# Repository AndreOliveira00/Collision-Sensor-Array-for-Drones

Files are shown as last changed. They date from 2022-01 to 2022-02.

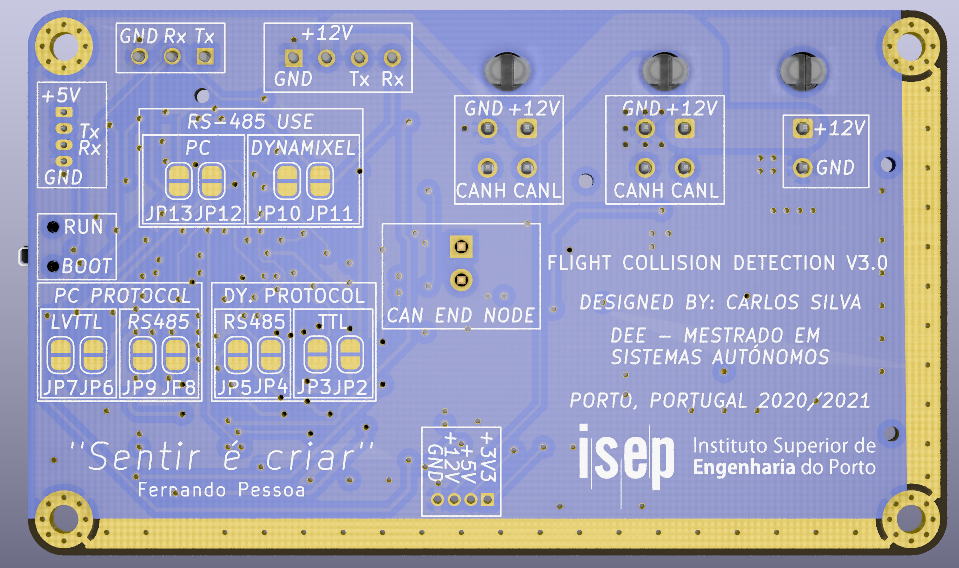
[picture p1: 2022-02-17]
Collision-Avoidance-System by CarlosVieira99/Collision-Avoidance-System/Images/Screenshot from 2021-01-22 17-19-14.png

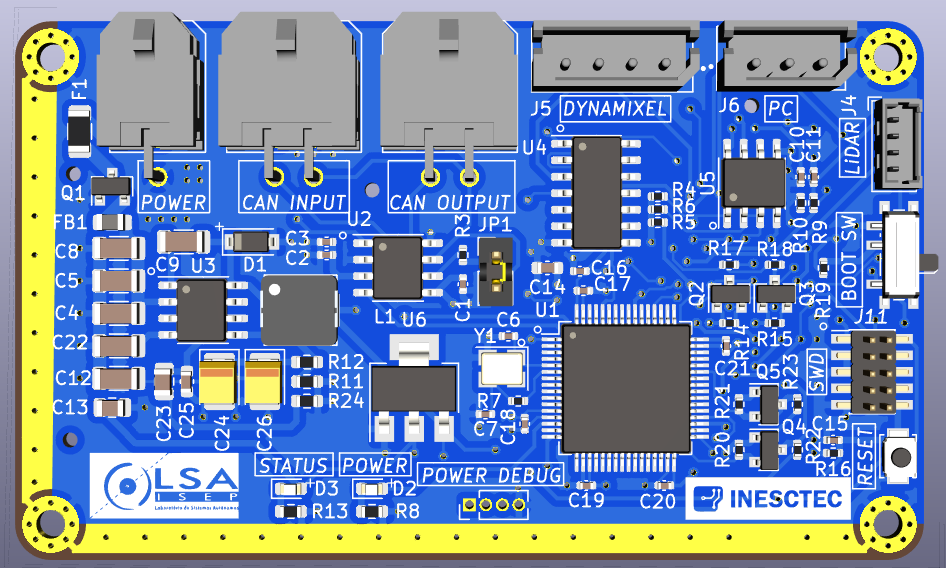
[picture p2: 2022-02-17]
Collision-Avoidance-System by CarlosVieira99/Collision-Avoidance-System/Images/Screenshot from 2021-01-22 17-07-21.png

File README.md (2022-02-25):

# Collision Sensor Array for Drones
 Collision Sensor Array for Drones using ToF and Solid State LiDAR

Este repositório contém o relatório do projeto desenvolvido no mestrado de Sistemas Autônomos na Unidade curricular LaSET. 
Imagens ilustrativas da PCB final e o desenvolvimento associado.

<b>RESUMO DO PROJETO:</b>

Para outros esclarecimentos contacte pelo email 1181045@isep.ipp.pt.

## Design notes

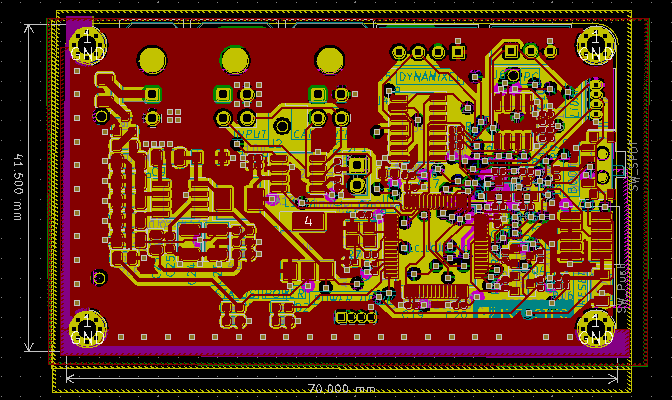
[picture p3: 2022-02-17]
Collision-Avoidance-System by CarlosVieira99/Collision-Avoidance-System/Images/Screenshot from 2021-01-22 17-06-26.png

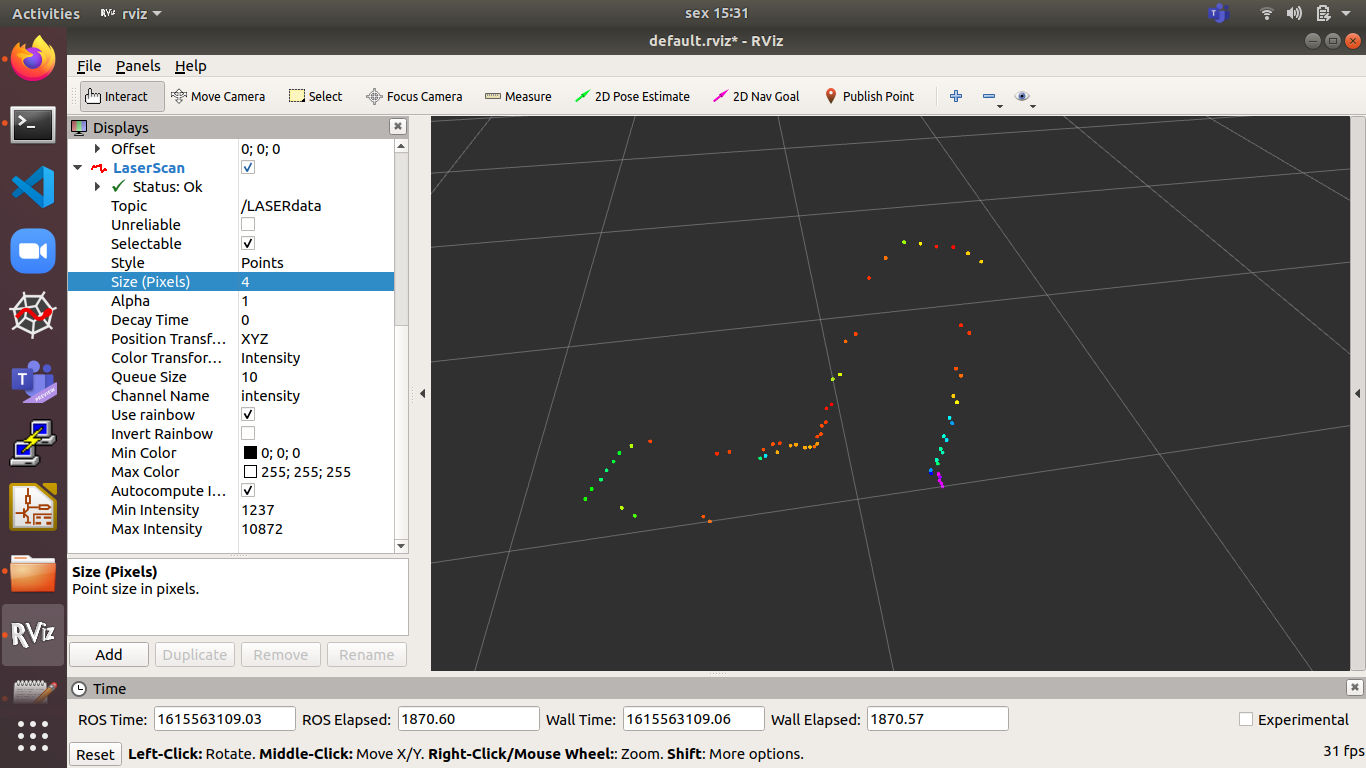
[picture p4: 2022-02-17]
Collision-Avoidance-System by CarlosVieira99/Collision-Avoidance-System/Images/Screenshot from 2021-03-12 15-31-49.png

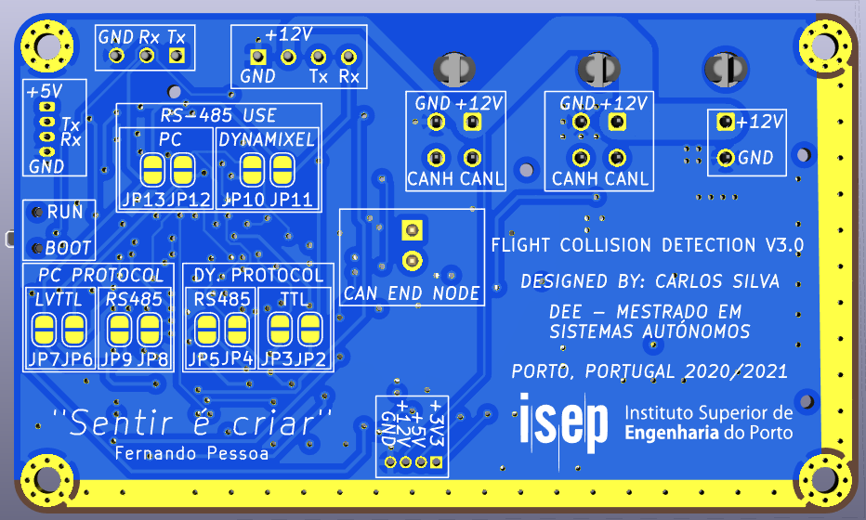
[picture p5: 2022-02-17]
Collision-Avoidance-System by CarlosVieira99/Collision-Avoidance-System/Images/Screenshot from 2021-01-22 17-07-58.png

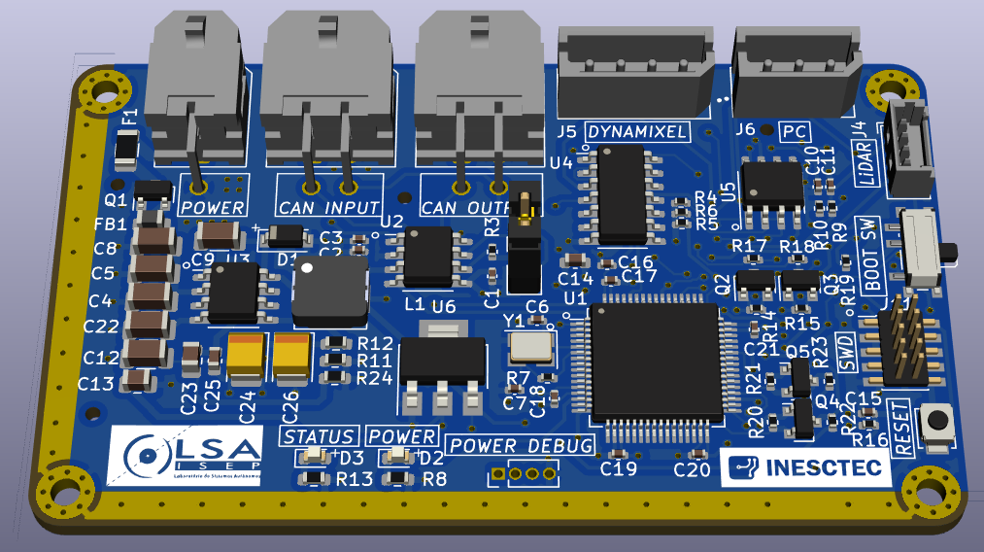
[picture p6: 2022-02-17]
Collision-Avoidance-System by CarlosVieira99/Collision-Avoidance-System/Images/Screenshot from 2021-01-22 17-07-32.png

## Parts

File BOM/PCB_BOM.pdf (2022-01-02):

# Bill of Materials

2175 Salk Avenue
Project Title: Bill of Materials for PCB Document [PCB_Final.PcbDoc] | Suite 200
Project File Name: LASET_Prj.PrjPcb | Carlsbad, CA 92008
Assembly Variant: None | USA
Part Number | Description | Designator | Manufacture | Manufacture Part Number | Supplier | Supplier Part Number | Supplier Unit Price | Quantity
CMP-2006-02256-2 | CAP CER 4.7UF 6.3V X5R 0603 | C1 | | | | | | | 1
CMP-0687-00068-1 | Aluminum Electrolytic Capacitor, UD Series, Low Impedance, 330 uF, 25 V, + / - 20%, -55 to 105 degC, Chip Type, 8 x 10 mm D x L, Pb-Free, Reel | C2 | | | | | | | 1
CMP-2007-04514-1 | | C3 | | | | | | | 1
CMP-2000-04991-1 | Chip Capacitor, 1 uF, +/-10%, 25 V, -55 to 125 degC, 1206 (3216 Metric), RoHS, Tape and Reel | C4 | | | | | | | 1
CMP-2100-03689-1 | Standard Tantalum, 22 uF, +/ - 10%, 16 V, -55 to 125 degC, 2-Pin SMD (1210), RoHS, Tape and Reel | C5 | | | | | | | 1
T491A106K020ATCapacitor Polarised | | C6, C7 | | | | | | | 2
CMP-08246-003443-1 | Multilayer Ceramic Capacitors 10uF ±10% 16V X5R SMD 1206 | C8, C23 | | | | | | | 2
CMP-2100-03641-2 | CAP CER 0.1UF 16V X7R 0402 | C9, C22 | | | | | | | 2
CMP-2006-02448-10603 | | C10, C11 | | | | | | | 2
CMP-2006-04264-1 | | C12, C13 | | | | | | | 2
CMP-1035-02737-2CAP CER 1UF 16V X5R 0603 | | C15 | | | | | | | 1
CMP-2100-03601-2 | CAP CER 0.1UF 50V X7R 0603 | C16, C17, C18, C19, C20, C21 | | | | | | | 6
SMAJ8.5A-M3_61TVS Diode (Uni-directional) | | D1, D5, D6 | | | | | | | 3
CMP-02520-000009-1 LED GREEN 0603 SMD | | D2, D3, D4 | | | | | | | 3
SF-0603SA200M-2Fuse | | F1 | | | | | | | 1
MMZ1608S601ATD25 Ferrite Bead | | FB1 | | | | | | | 1
CMP-1387-00004-1 | SMD Power Inductor WE-PD HV, L=1000 µH | L1, L2 | | | | | | | 2
V7805-2000 | Power Supply | P1 | | | | | | | 1
LM1117DT-3.3_NOPB Integrated Circuit | | P2 | | | | | | | 1
22-12-4022 | Connector | P3 | | | | | | | 1
CMP-1502-01064-1 | THT Vertical Pin Header WR-PHD, Pitch 2.54 mm, Single Row, 4 pins | P4 | | | | | | | 1
53048-0410 | Connector | P6, P7, P8, P9, P10, P11, P12, P13 | | | | | | | 8
M50-3530642 | Connector | P14 | | | | | | | 1
22-28-4046 | Connector | P15 | | | | | | | 1
22-03-5045 | Connector | P16, P17 | | | | | | | 2
22-03-5035 | Connector | P18 | | | | | | | 1
SI2301BDS-T1-BE3Integrated Circuit | | Q1 | | | | | | | 1
CMP-2000-00897-1 | | R1, R18, R24, R25 | | | | | | | 4
CMP-2000-00897-1 | | R2, R5, R19, R20, R21, R28 | | | | | | | 6
CMP-2000-00897-1 | | R3 | | | | | | | 1
CMP-2000-00897-1 | | R4, R6, R10 | | | | | | | 3
CMP-2000-05022-1 | Resistor, 10 kOhm, +/- 5%, 100 mW, -55 to 155 degC, 0603 (1608 Metric), RoHS, Tape and Reel | R7, R8 | | | | | | | 2
CMP-2100-03667-1 | Chip Resistor, 0 Ohm, +/-5%, 0.1 W, -55 to 155 degC, 0603 (1608 Metric), RoHS, Tape and Reel | R9, R11, R12, R15, R16 | | | | | | | 5
CMP-2100-03667-1 | Chip Resistor, 0 Ohm, +/-5%, 0.1 W, -55 to 155 degC, 0603 (1608 Metric), RoHS, Tape and Reel | R13, R14 | | | | | | | 2
CMP-2000-00897-1 | | R17 | | | | | | | 1
CMP-2000-00897-1 | | R22, R23 | | | | | | | 2
CMP-2000-00897-1 | | R26, R27 | | | | | | | 2
CMP-03402-000005-1 | SWITCH TACTILE SPST-NO 0.05A 24V | SW1 | | | | | | | 1
CMP-2000-06884-2 | SWITCH SLIDE SPDT 300MA 6V | SW2 | | | | | | | 1
STM32F103RBT6 No Description Available | | U1 | | | | | | | 1
CMP-0310-00139-2 | Differential Bus Transceiver, 1 TX / 1 RX, 5V, 0 to 70 degC, 8-Pin SOIC (D), Green (RoHS & no Sb/Br) | U2 | | | | | | | 1
TJA1051T_3_CM,118 Integrated Circuit | | U3 | | | | | | | 1
CMP-2000-05036-1 | Low Frequency Crystal, 32.768 KHz, 6 pF, +/- 20 ppm, -40 to 85 degC, 4-Pin SMD, RoHS, Tape and Reel | X1 | | | | | | | 1
CMP-1749-00003-1 | Resistance Weld Thru-Hole Crystal, 16 MHz, -20 to 70 degC, 2-Pin THD, RoHS, Bulk | X2 | | | | | | | 1
1SMB5921BT3G | Zener Diode | Z1 | | | | | | | 1
| $0,00 86
Approved | Notes

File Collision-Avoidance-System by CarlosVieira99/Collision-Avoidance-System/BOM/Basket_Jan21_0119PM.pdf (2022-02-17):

# Privacy policy and cookies

Mouser Electronics uses cookies and similar technologies to help deliver the best experience on our site. Our cookies are necessary for the operation of the website, monitoring site performance and to deliver relevant content. You can visit our Privacy Centre (https://pt.mouser.com/Cart/%5Cprivacypolicy) to learn more about your online settings.

## Accept & Close

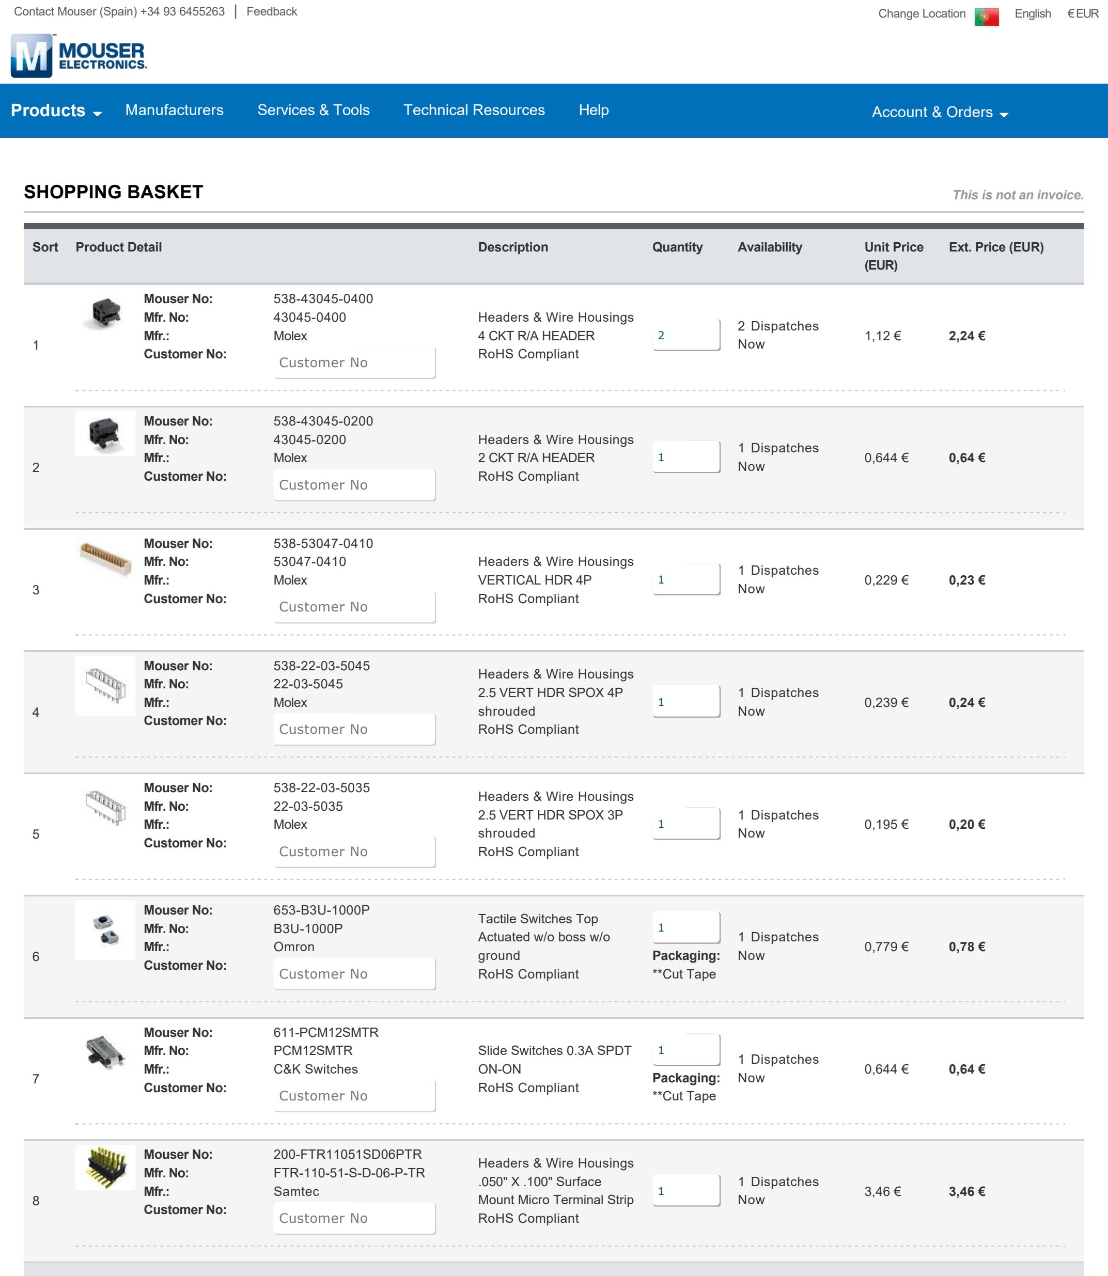
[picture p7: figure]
Mouser No:; Mfr. No:; Mfr.:; Molex; Customer No:; Omron; 611-PCM12SMTR; PCM12SMTR; C&K Switches; 200-FTR11051SD06PTR; FTR-110-51-S-D-06-P-TR; Samtec; Sort; Product Detail; Description; Quantity; Availability; Unit Price; (EUR); Ext. Price (EUR); SHOPPING BASKET; This is not an invoice.; Headers & Wire Housings; 4 CKT R/A HEADER; RoHS Compliant; 2 Dispatches; Now; 2 CKT R/A HEADER; 1 Dispatches; VERTICAL HDR 4P; 2.5 VERT HDR SPOX 4P; shrouded; 2.5 VERT HDR SPOX 3P; Tactile Switches Top; Actuated w/o boss w/o; ground; Packaging:; **Cut Tape; Slide Switches 0.3A SPDT; .050" X .100" Surface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

Products (https://pt.mouser.com/Electronic-Components/) | Manufacturers (https://pt.mouser.com/manufacturer/) | Services & Tools (https://pt.mouser.com/servicesandtools/) | Technical Resources (https://pt.mouser.com/technical-resources/) | Help (https://pt.mouser.com/Help/Help.aspx) | Account & Orders (https://pt.mouser.com/MyMouser/AccountSummary.aspx)
Contact Mouser (Spain) +34 93 6455263 (https://pt.mouser.com/contact/) | Feedback (https://pt.mouser.com/feedback.aspx) | Change Location (https://pt.mouser.com/cs/localsites/) | English | € EUR

By submitting your order you agree to these terms and conditions. (https://pt.mouser.com/saleterms) For additional information on availability, click on the Mouser Part No.

**All MouseReel™ items are noncancellable and nonreturnable.

Incoterms:DDP
All prices include duty and customs fees on select shipping methods. Free shipping on most orders over 50 € (EUR)
Merchandise: | | 8,43 €
Shipping: | FedEx International Priority | 20,00 €
| + More Delivery Options (https://pt.mouser.com/Cart/Cart/CartShipEstimate/)
Subtotal: | | 28,43 €

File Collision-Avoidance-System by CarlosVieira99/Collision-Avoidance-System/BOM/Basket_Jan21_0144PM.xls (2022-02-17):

SHOPPING BASKET
This is not an invoice
21-Jan-21 13:44:50
 | Mouser No | Mfr. No | Manufacturer | Customer No | Description | RoHS | Lifecycle | Order Qty. | Price (EUR) | Ext.: (EUR)
1 | 538-43045-0400 | 43045-0400 | Molex |  | Headers & Wire Housings 4 CKT R/A HEADER | RoHS Compliant |  | 2 | 1,12 € | 2,24 €
2 | 538-43045-0200 | 43045-0200 | Molex |  | Headers & Wire Housings 2 CKT R/A HEADER | RoHS Compliant |  | 1 | 0,644 € | 0,64 €
3 | 538-53047-0410 | 53047-0410 | Molex |  | Headers & Wire Housings VERTICAL HDR 4P | RoHS Compliant |  | 1 | 0,229 € | 0,23 €
4 | 538-22-03-5045 | 22-03-5045 | Molex |  | Headers & Wire Housings 2.5 VERT HDR SPOX 4P shrouded | RoHS Compliant |  | 1 | 0,239 € | 0,24 €
5 | 538-22-03-5035 | 22-03-5035 | Molex |  | Headers & Wire Housings 2.5 VERT HDR SPOX 3P shrouded | RoHS Compliant |  | 1 | 0,195 € | 0,20 €
6 | 653-B3U-1000P | B3U-1000P | Omron |  | Tactile Switches Top Actuated w/o boss w/o ground | RoHS Compliant |  | 1 | 0,779 € | 0,78 €
7 | 611-PCM12SMTR | PCM12SMTR | C&K Switches |  | Slide Switches 0.3A SPDT ON-ON | RoHS Compliant |  | 1 | 0,644 € | 0,64 €
8 | 200-FTR11051SD06PTR | FTR-110-51-S-D-06-P-TR | Samtec |  | Headers & Wire Housings .050" X .100" Surface Mount Micro Terminal Strip | RoHS Compliant |  | 1 | 3,46 € | 3,46 €
By submitting your order you agree to these terms and conditions. (https://pt.mouser.com/saleterms) |  |  |  |  |  |  |  |  | Merchandise: | 8,43 €
Prices are reflected at the date and time shown. |  |  |  |  |  |  |  |  | Delivery Charge: | 20,00 €

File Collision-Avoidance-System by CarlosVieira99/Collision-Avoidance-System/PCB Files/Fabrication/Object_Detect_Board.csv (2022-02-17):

Comment | Designator | Footprint | LCSC
0.1u | C1,C2,C11 | Capacitor_SMD:C_0402_1005Metric
10u | C3,C10 | Capacitor_SMD:C_0402_1005Metric
0.1u | C9,C12 | Capacitor_SMD:C_1206_3216Metric
22uF | C13 | Capacitor_SMD:C_0805_2012Metric
4u7 | C14 | Capacitor_SMD:C_0603_1608Metric
100n | C15,C16,C17,C18,C19,C20,C21 | Capacitor_SMD:C_0402_1005Metric
4700p | C23 | Capacitor_SMD:C_0805_2012Metric
33u | C24,C26 | Capacitor_Tantalum_SMD:CP_EIA-3528-21_Kemet-B
39p | C25 | Capacitor_SMD:C_0603_1608Metric
4u7 | C4,C5 | Capacitor_SMD:C_1206_3216Metric
12p | C6,C7 | Capacitor_SMD:C_0402_1005Metric
0.01u | C8,C22 | Capacitor_SMD:C_1206_3216Metric
B5819W | D1 | Diode_SMD:D_SOD-123
BLUE | D2 | LED_SMD:LED_0603_1608Metric
GREEN | D3 | LED_SMD:LED_0603_1608Metric
1.2A | F1 | Fuse:Fuse_1206_3216Metric
600@600MHz | FB1 | Inductor_SMD:L_0805_2012Metric
M2 | H1,H2,H3,H4 | MountingHole:MountingHole_2.2mm_M2_Pad_Via
Power_Input_12V | J1 | Connector_Molex:Molex_Micro-Fit_3.0_43045-0200_2x01_P3.00mm_Horizontal
SWD | J11 | Connector_PinHeader_1.27mm:PinHeader_2x05_P1.27mm_Vertical_SMD
CAN_IN | J2 | Connector_Molex:Molex_Micro-Fit_3.0_43045-0400_2x02_P3.00mm_Horizontal
CAN_OUT | J3 | Connector_Molex:Molex_Micro-Fit_3.0_43045-0400_2x02_P3.00mm_Horizontal
LiDAR | J4 | Connector_Molex:Molex_PicoBlade_53047-0410_1x04_P1.25mm_Vertical
DYNAMIXEL | J5 | local:MOLEX_22-03-5045
PC | J6 | local:MOLEX_22-03-5035
Debug Hardware | J7 | Connector_PinHeader_1.27mm:PinHeader_1x04_P1.27mm_Vertical
Jumper_2_Open | JP1 | Connector_PinHeader_2.54mm:PinHeader_1x02_P2.54mm_Vertical
SolderJumper_2_Open | JP2,JP3,JP4,JP5,JP6,JP7,JP8,JP9,JP10,JP11,JP12,JP13 | Jumper:SolderJumper-2_P1.3mm_Open_RoundedPad1.0x1.5mm
10u | L1 | Inductor_SMD:L_Sunlord_MWSA0518_5.4x5.2mm
AO3401A | Q1 | Package_TO_SOT_SMD:SOT-23
BSS138 | Q2,Q3,Q4,Q5 | Package_TO_SOT_SMD:SOT-23
49.9k | R11 | Resistor_SMD:R_0603_1608Metric
10k | R12 | Resistor_SMD:R_0603_1608Metric
220 | R13 | Resistor_SMD:R_0603_1608Metric
10k | R4,R5,R6,R14,R15,R16,R17,R18,R19,R20,R21,R22,R23 | Resistor_SMD:R_0402_1005Metric
1.91k | R24 | Resistor_SMD:R_0603_1608Metric
120 | R3 | Resistor_SMD:R_0402_1005Metric
47 | R7 | Resistor_SMD:R_0402_1005Metric
1k | R8 | Resistor_SMD:R_0603_1608Metric
20k | R9,R10 | Resistor_SMD:R_0402_1005Metric
SW_Push | SW1 | Button_Switch_SMD:SW_SPST_B3U-1000P
SW_SPDT | SW2 | Button_Switch_SMD:SW_SPDT_PCM12
STM32F103RBTx | U1 | Package_QFP:LQFP-64_10x10mm_P0.5mm
TJA1051T-3 | U2 | Package_SO:SOIC-8_3.9x4.9mm_P1.27mm
TPS54331 | U3 | Package_SO:SOIC-8_3.9x4.9mm_P1.27mm
74HC126 | U4 | Package_SO:SOIC-14_3.9x8.7mm_P1.27mm
SN75176AD | U5 | Package_SO:SOIC-8_3.9x4.9mm_P1.27mm
AMS1117-3.3 | U6 | Package_TO_SOT_SMD:SOT-223
16 MHz | Y1 | Crystal:Crystal_SMD_3225-4Pin_3.2x2.5mm

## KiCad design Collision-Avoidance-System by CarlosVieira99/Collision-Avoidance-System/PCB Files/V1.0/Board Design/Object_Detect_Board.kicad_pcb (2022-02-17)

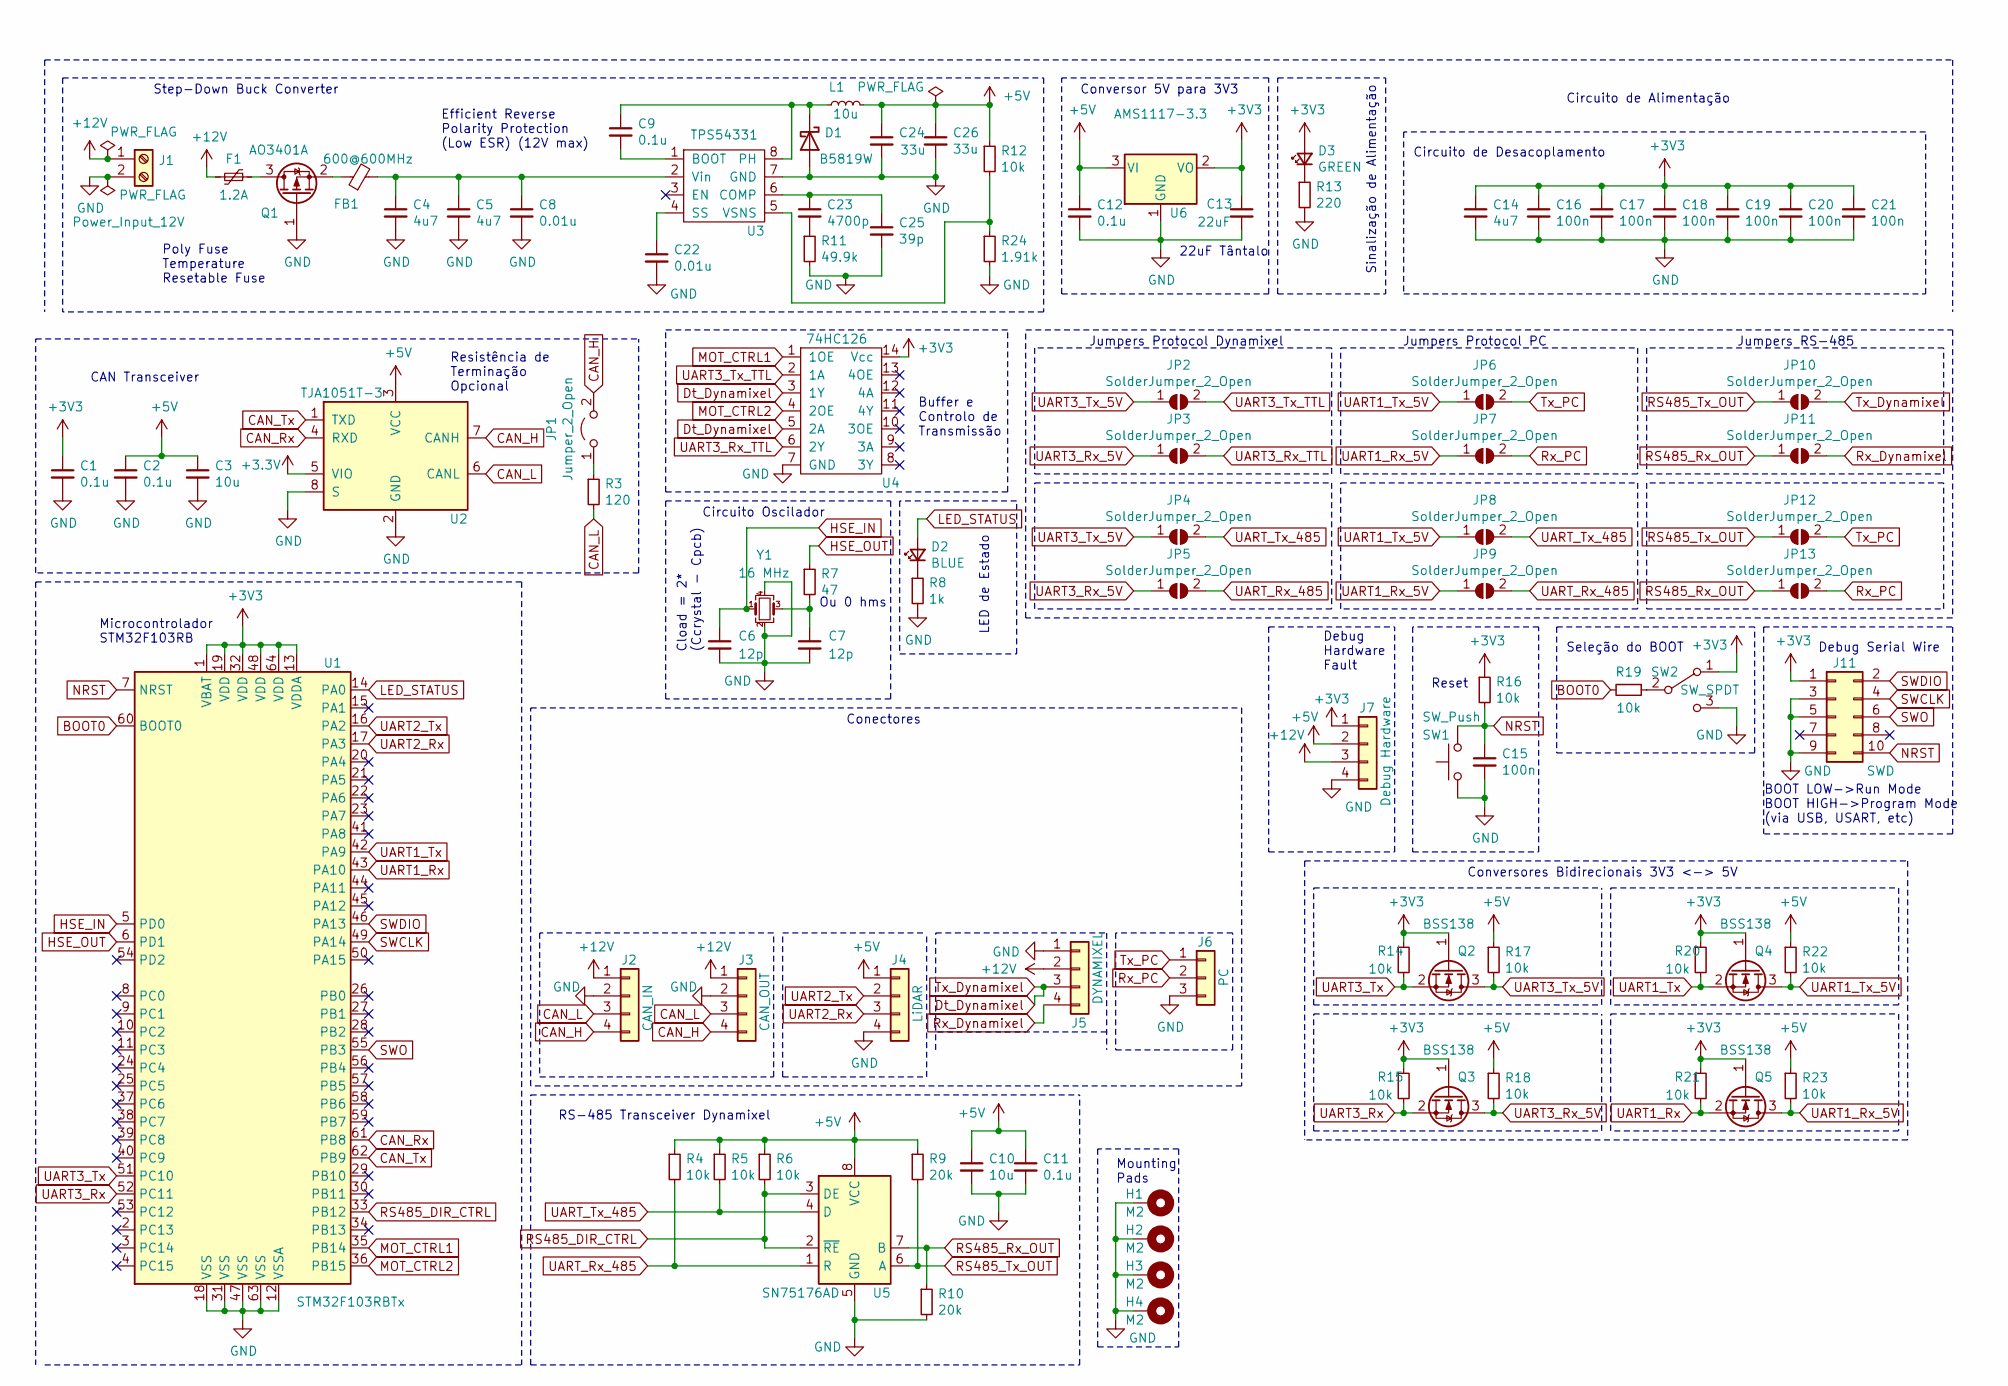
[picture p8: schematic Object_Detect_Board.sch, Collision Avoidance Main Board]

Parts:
C1, C2, C11: 0.1u; C_0402_1005Metric; LCSC Part # C1525
C3, C10: 10u; C_0402_1005Metric; LCSC Part # C15525
C4, C5: 4u7; C_1206_3216Metric; LCSC Part # C29823
C6, C7: 12p; C_0402_1005Metric; LCSC Part # C1547
C8, C22: 0.01u; C_1206_3216Metric; LCSC Part # C1846
C9, C12: 0.1u; C_1206_3216Metric; LCSC Part # C24497
C13: 22uF; C_0805_2012Metric; LCSC Part # C45783
C14: 4u7; C_0603_1608Metric; LCSC Part # C19666
C15, C16, C17, C18, C19, C20, C21: 100n; C_0402_1005Metric; LCSC Part # C1525
C23: 4700p; C_0805_2012Metric; LCSC Part # C1744
C24, C26: 33u; CP_EIA-3528-21_Kemet-B; LCSC Part # C139576
C25: 39p; C_0603_1608Metric; LCSC Part # C53278
D1: B5819W; D_SOD-123; LCSC Part # C8598
D2: BLUE; LED_0603_1608Metric; LCSC Part # C72041
D3: GREEN; LED_0603_1608Metric; LCSC Part # C72043
F1: 1.2A; Fuse_1206_3216Metric; LCSC Part # C70082
FB1: 600@600MHz; L_0805_2012Metric; LCSC Part # C1017
H1, H2, H3, H4: M2; MountingHole_2.2mm_M2_Pad_Via
J1: Power_Input_12V; Molex_Micro-Fit_3.0_43045-0200_2x01_P3.00mm_Horizontal; LCSC Part C29823
J2: CAN_IN; Molex_Micro-Fit_3.0_43045-0400_2x02_P3.00mm_Horizontal
J3: CAN_OUT; Molex_Micro-Fit_3.0_43045-0400_2x02_P3.00mm_Horizontal
J4: LiDAR; Molex_PicoBlade_53047-0410_1x04_P1.25mm_Vertical
J5: DYNAMIXEL; MOLEX_22-03-5045
J6: PC; MOLEX_22-03-5035
J7: Debug Hardware; PinHeader_1x04_P1.27mm_Vertical
J11: SWD; PinHeader_2x05_P1.27mm_Vertical_SMD
JP1: Jumper_2_Open; PinHeader_1x02_P2.54mm_Vertical
JP2, JP3, JP4, JP5, JP6, JP7, JP8, JP9, JP10, JP11, JP12, JP13: SolderJumper_2_Open; SolderJumper-2_P1.3mm_Open_RoundedPad1.0x1.5mm
L1: 10u; L_Sunlord_MWSA0518_5.4x5.2mm; LCSC Part # C408412
Q1: AO3401A; SOT-23; LCSC Part # C15127
Q2, Q3, Q4, Q5: BSS138; SOT-23; LCSC Part # C112239
R3: 120; R_0402_1005Metric; LCSC Part # C25079
R4, R5, R6, R14, R15, R16, R17, R18, R19, R20, R21, R22, R23: 10k; R_0402_1005Metric; LCSC Part # C25744
R7: 47; R_0402_1005Metric; LCSC Part # C25118
R8: 1k; R_0603_1608Metric; LCSC Part # C21190
R9, R10: 20k; R_0402_1005Metric; LCSC Part # C25765
R11: 49.9k; R_0603_1608Metric; LCSC Part # C23184
R12: 10k; R_0603_1608Metric; LCSC Part # C25804
R13: 220; R_0603_1608Metric; LCSC Part # C22962
R24: 1.91k; R_0603_1608Metric; LCSC Part # C22853
SW1: SW_Push; SW_SPST_B3U-1000P
SW2: SW_SPDT; SW_SPDT_PCM12
U1: STM32F103RBTx; LQFP-64_10x10mm_P0.5mm; LCSC Part # C8735
U2: TJA1051T-3; SOIC-8_3.9x4.9mm_P1.27mm; LCSC Part # C38695
U3: TPS54331; SOIC-8_3.9x4.9mm_P1.27mm; LCSC Part # C9865
U4: 74HC126; SOIC-14_3.9x8.7mm_P1.27mm; LCSC Part # C5600
U5: SN75176AD; SOIC-8_3.9x4.9mm_P1.27mm; LCSC Part # C7063
U6: AMS1117-3.3; SOT-223; LCSC Part # C6186
Y1: 16 MHz; Crystal_SMD_3225-4Pin_3.2x2.5mm; LCSC Part # C13738

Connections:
+5V: C2.1, C3.1, C10.1, C11.1, C12.1, C24.1, C26.1, J4.1, J7.2, L1.2, R4.1, R5.1, R6.1, R9.1, R12.1, R17.1, R18.1, R22.1, R23.1, U2.3 (VCC), U5.8 (VCC), U6.3 (VI); also elsewhere on the board
+12V: F1.2, J1.1, J2.1, J3.1, J5.2, J7.3; also elsewhere on the board
BOOT0: R19.2, U1.60 (BOOT0)
CAN_H: J2.4, J3.4, JP1.2 (B), U2.7 (CANH)
CAN_L: J2.3, J3.3, R3.2, U2.6 (CANL)
CAN_Rx: U1.61 (PB8), U2.4 (RXD)
CAN_Tx: U1.62 (PB9), U2.1 (TXD)
Dt_Dynamixel: J5.3, JP10.2 (B), U4.3 (1Y), U4.5 (2A)
GND: C1.2, C2.2, C3.2, C4.2, C5.2, C6.2, C7.2, C8.2, C10.2, C11.2, C12.2, C13.2, C14.2, C15.2, C16.2, C17.2, C18.2, C19.2, C20.2, C21.2, C22.2, C24.2, C25.2, C26.2, D1.2 (A), H1.1, H2.1, H3.1, H4.1, J1.2, J2.2, J3.2, J4.4, J5.1, J6.3, J7.4, J11.3, J11.5, J11.9, Q1.1 (G), R8.2, R10.2, R11.2, R13.2, R24.2, SW1.1, SW2.3 (C), U1.12 (VSSA), U1.18 (VSS), U1.31 (VSS), U1.47 (VSS), U1.63 (VSS), U2.2 (GND), U2.8 (S), U3.7 (GND), U4.7 (GND), U5.5 (GND), U6.1 (GND), Y1.2, Y1.4; also elsewhere on the board
HSE_IN: C6.1, U1.5 (PD0), Y1.1
HSE_OUT: R7.1, U1.6 (PD1)
LED_STATUS: D2.2 (A), U1.14 (PA0)
MOT_CTRL1: U1.35 (PB14), U4.1 (1OE)
MOT_CTRL2: U1.36 (PB15), U4.4 (2OE)
NRST: C15.1, J11.10, R16.2, SW1.2, U1.7 (NRST); also elsewhere on the board
unnamed: C4.1, C5.1, C8.1, FB1.2, U3.2 (Vin)
unnamed: C7.1, R7.2, Y1.3
unnamed: C9.1, D1.1 (K), L1.1, U3.8 (PH)
unnamed: C9.2, U3.1 (BOOT)
unnamed: C22.1, U3.4 (SS)
unnamed: C23.1, C25.1, U3.6 (COMP)
unnamed: C23.2, R11.1
unnamed: D2.1 (K), R8.1
unnamed: D3.1 (K), R13.1
unnamed: F1.1, Q1.3 (D)
unnamed: FB1.1, Q1.2 (S)
unnamed: JP1.1 (A), R3.1
unnamed: R12.2, R24.1, U3.5 (VSNS)
unnamed 30: R19.1, SW2.2 (B); also elsewhere on the board
RS485_DIR_CTRL: R6.2, U1.33 (PB12), U5.2 (~RE), U5.3 (DE)
RS485_Rx_OUT: JP11.1 (A), JP13.1 (A), R10.1, U5.7 (B)
RS485_Tx_OUT: JP10.1 (A), JP12.1 (A), R9.2, U5.6 (A)
Rx_Dynamixel: J5.4, JP11.2 (B)
Rx_PC: J6.2, JP7.2 (B), JP13.2 (B)
SWCLK: J11.4, U1.49 (PA14)
SWDIO: J11.2, U1.46 (PA13)
SWO: J11.6, U1.55 (PB3)
Tx_PC: J6.1, JP6.2 (B), JP12.2 (B)
UART1_Rx: Q5.2 (S), R21.2, U1.43 (PA10)
UART1_Rx_5V: JP7.1 (A), JP9.1 (A), Q5.3 (D), R23.2
UART1_Tx: Q4.2 (S), R20.2, U1.42 (PA9)
UART1_Tx_5V: JP6.1 (A), JP8.1 (A), Q4.3 (D), R22.2
UART2_Rx: J4.3, U1.17 (PA3)
UART2_Tx: J4.2, U1.16 (PA2)
UART3_Rx: Q3.2 (S), R15.2, U1.52 (PC11)
UART3_Rx_5V: JP3.1 (A), JP5.1 (A), Q3.3 (D), R18.2
UART3_Rx_TTL: JP3.2 (B), U4.6 (2Y)
UART3_Tx: Q2.2 (S), R14.2, U1.51 (PC10)
UART3_Tx_5V: JP2.1 (A), JP4.1 (A), Q2.3 (D), R17.2
UART3_Tx_TTL: JP2.2 (B), U4.2 (1A)
UART_Rx_485: JP5.2 (B), JP9.2 (B), R4.2, U5.1 (R)
UART_Tx_485: JP4.2 (B), JP8.2 (B), R5.2, U5.4 (D)

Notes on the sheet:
BOOT LOW->Run Mode BOOT HIGH->Program Mode (via USB, USART, etc)
Cload = 2* (Ccrystal - Cpcb)
Ou 0 hms
22uF Tântalo
Circuito Oscilador
Debug Serial Wire
Seleção do BOOT
Circuito de Alimentação
Conversor 5V para 3V3
Sinalização de Alimentação
Microcontrolador STM32F103RB
Circuito de Desacoplamento
Buffer e Controlo de Transmissão
Debug Hardware Fault
Poly Fuse Temperature Resetable Fuse
Efficient Reverse Polarity Protection (Low ESR) (12V max)
CAN Transceiver
Resistência de Terminação Opcional
Conversores Bidirecionais 3V3 <-> 5V
RS-485 Transceiver Dynamixel
LED de Estado
Mounting Pads
Jumpers Protocol Dynamixel
Jumpers Protocol PC
Jumpers RS-485
Reset
Step-Down Buck Converter
Conectores

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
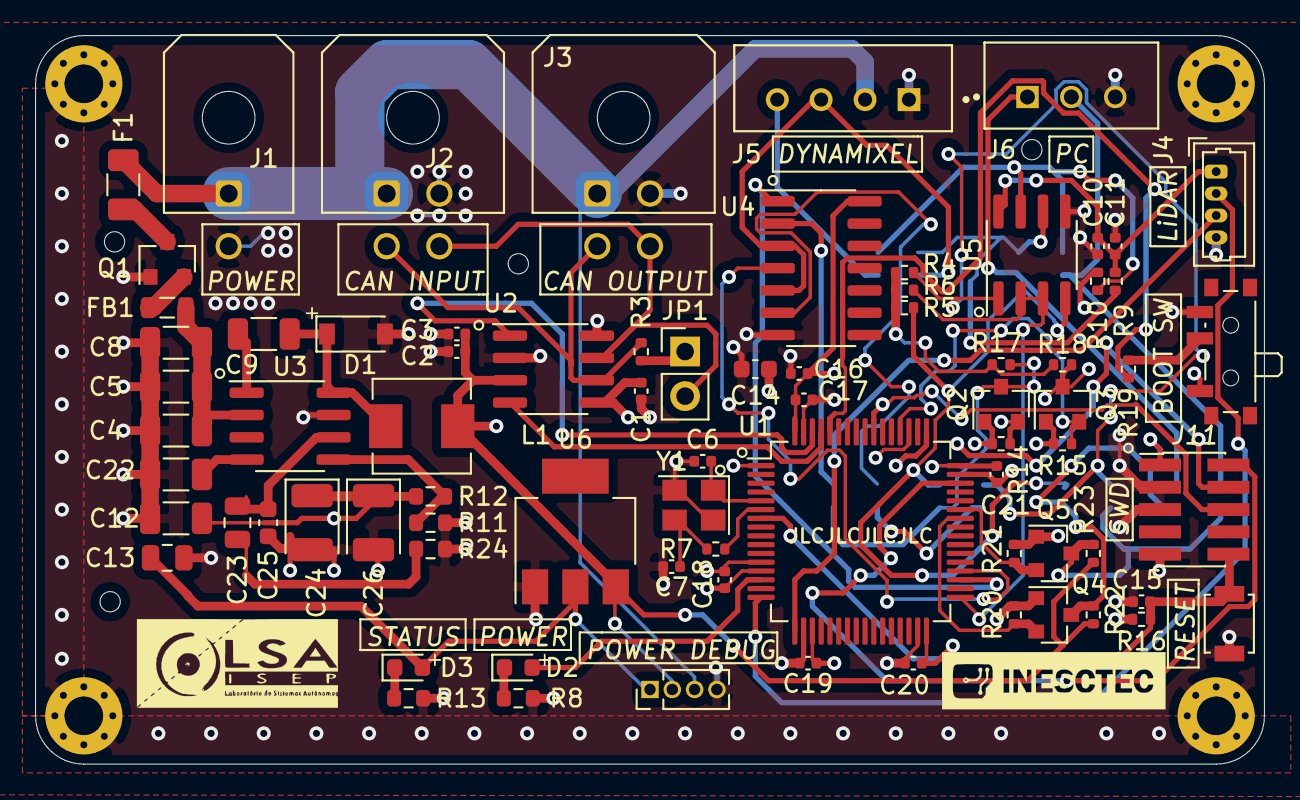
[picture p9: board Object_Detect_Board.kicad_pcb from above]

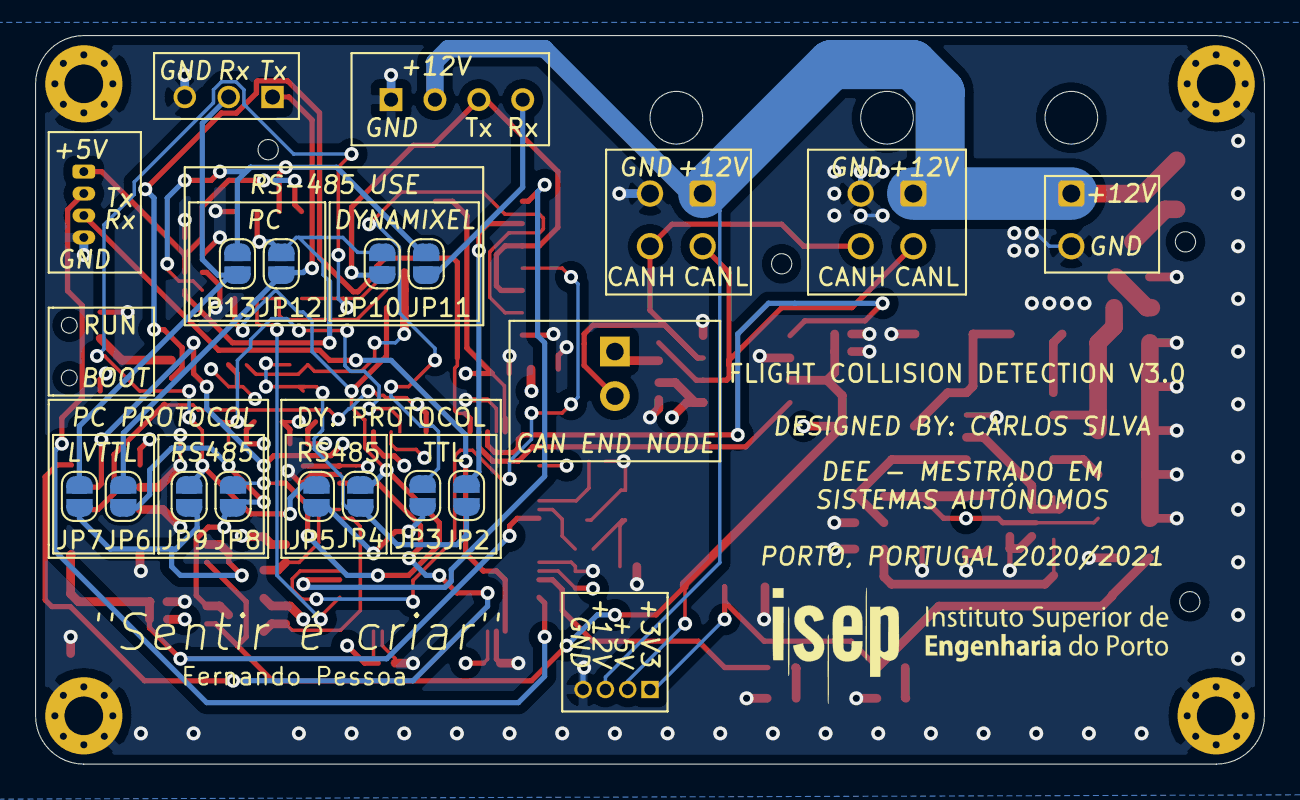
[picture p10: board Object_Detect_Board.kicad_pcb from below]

Board: 4 copper layers, 70.0 x 41.5 mm, 93 parts (12 on the bottom side), 53 nets.

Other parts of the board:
BOOT SW: SW_SPDT; SW_SPDT_PCM12
POWER DEBUG: Debug Hardware; PinHeader_1x04_P1.27mm_Vertical
RESET: SW_Push; SW_SPST_B3U-1000P

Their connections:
+5V: POWER DEBUG.2; also elsewhere on the board
+12V: POWER DEBUG.3; also elsewhere on the board
GND: BOOT SW.3, POWER DEBUG.4, RESET.1; also elsewhere on the board
NRST: RESET.2; also elsewhere on the board
unnamed 30: BOOT SW.2; also elsewhere on the board

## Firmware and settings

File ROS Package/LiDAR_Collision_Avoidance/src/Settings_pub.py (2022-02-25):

#!/usr/bin/env python3

import time
import rospy
from pynput import keyboard
from LiDAR_Collision_Avoidance.msg import Settings
import os



class LiDAR_Control:

    def __init__(self) :

        rospy.init_node('LiDAR_Control' , anonymous=False)

        self.Setting_topic= rospy.Publisher('LiDAR_Collision_Avoidance' +  '/Settings/',  Settings, queue_size=100)
        self.Settings_msg= Settings()
        self.Settings_msg.slave_id=48

        self.rate = rospy.Rate(1)
        self.tick_step=300
        self.initial_tick=1500
        self.final_tick=2048
        self.frequency=50
        self.print_banner()

    def main(self):
    
        while not rospy.is_shutdown():
            with keyboard.Events() as events:
                event = events.get(1e6)
                self.Command(event.key)
                self.print_banner()
                self.Settings_msg.initial_tick = self.initial_tick
                self.Settings_msg.final_tick = self.final_tick
                self.Settings_msg.tick_step = self.tick_step
                self.Settings_msg.frequency = self.frequency
                self.Setting_topic.publish(self.Settings_msg)
 

    def Command(self,key):

        if key == keyboard.KeyCode.from_char('q'):
            if(self.tick_step >= 1 ):
                self.tick_step = self.tick_step-40
                
        if key == keyboard.KeyCode.from_char('e'):
            if(self.tick_step <= 800 ):
                self.tick_step = self.tick_step+40   
        
        if key == keyboard.KeyCode.from_char('d'):
            self.initial_tick = self.initial_tick-128
            self.final_tick = self.final_tick-128
            if(self.initial_tick < 0 ):
                self.final_tick = self.final_tick-self.initial_tick
                self.initial_tick = 0
                
        if key == keyboard.KeyCode.from_char('a'):
            self.initial_tick = self.initial_tick+128
            self.final_tick = self.final_tick+128
            if(self.final_tick > 4096 ):
                self.initial_tick = self.initial_tick-( self.final_tick-4096 )
                self.final_tick = 4096 
            
        if key == keyboard.KeyCode.from_char('w'):
            self.initial_tick= self.initial_tick-16
            self.final_tick = self.final_tick+16
            
            if(self.final_tick > 4096 ):
                self.initial_tick = self.initial_tick-( self.final_tick-4096 )
                self.final_tick = 4096
                
            if(self.initial_tick < 0 ):
                self.final_tick = self.final_tick - self.initial_tick
                self.initial_tick=0
 
                
        if key == keyboard.KeyCode.from_char('s'):
            self.initial_tick = self.initial_tick+16
            self.final_tick = self.final_tick-16
            
            if(self.initial_tick > self.final_tick):
                self.initial_tick = self.final_tick
            
            if(self.final_tick > 4096 ):
                self.initial_tick = self.initial_tick - ( self.final_tick - 4096)
                self.final_tick = 4096
                
            if(self.initial_tick < 0 ):
                self.final_tick = self.final_tick - self.initial_tick
                self.initial_tick=0
                
                 
        if key == keyboard.KeyCode.from_char('+'):
           if(self.frequency <= 100 ):
               self.frequency = self.frequency+10    
              
               
        if key == keyboard.KeyCode.from_char('-'):
          if(self.frequency >= 1 ):
              self.frequency = self.frequency-10   
            
               
        time.sleep(2)

    def print_banner(self):

        clear = lambda: os.system('clear')
        clear()
        print("|============================================================================|")
        print("|============================MAPEAMENTO-DE-TECLAS============================|")
        print("|============================================================================|")
        print("|----------------------------------------------------------------------------|")
        print("| 's' ---> Diminuir o ângulo do scan                                         |")
        print("| 'w' ---> Aumentar o ângulo do scan                                         |")
        print("|----------------------------------------------------------------------------|")
        print("| 'a' ---> Rodar a posição angular de scan no sentido anti-horário           |")
        print("| 'd' ---> Rodar a posição angular de scan no sentido horário                |")
        print("|----------------------------------------------------------------------------|")
        print("| 'q' ---> Diminuir o tick de incremento                                     |")
        print("| 'e' ---> Aumentar o tick de incremento                                     |")
        print("|----------------------------------------------------------------------------|")
        print("| '-' ---> Diminuir a frequência de funcionamento                            |")
        print("| '+' ---> Diminuir a frequência de funcionamento                            |")
        print("|----------------------------------------------------------------------------|")
        print("|============================================================================|")
        print("|====================CONFIGURAÇÕES-DE-FUNCIONAMENTO-ATIVAS===================|")
        print("|============================================================================|")
        print("|----------------------------------------------------------------------------|")
        print("| Tick inical ---> ",self.initial_tick,"                                   ")
        print("|----------------------------------------------------------------------------|")
        print("| Tick Final ---> ",self.final_tick,"                                     ")
        print("|----------------------------------------------------------------------------|")
        print("| Tick de incremento ---> ",self.tick_step,"                                ")
        print("|----------------------------------------------------------------------------|")
        print("| Frequência de funcionamento ---> ",self.frequency,"                       ")
        print("|----------------------------------------------------------------------------|")
        print("|============================================================================|")
    


def start():
    LiDAR_control = LiDAR_Control()
    LiDAR_control.main()


if __name__ == '__main__':
    try:
        start()
        rospy.spin()
    except rospy.ROSInterruptException:

        pass
         
    

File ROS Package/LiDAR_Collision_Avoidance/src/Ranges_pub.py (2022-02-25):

#!/usr/bin/env python3

import time
import random
import rospy
import serial
import numpy as np
from sensor_msgs.msg import Range
from LiDAR_Collision_Avoidance.msg import Settings
import tf


class LiDAR_Collision_Avoidance:

    def __init__(self) :

        #/dev/ttyACM0
        self.ser = serial.Serial(
            port='/dev/ttyUSB0',\
            baudrate=115200,\
            parity=serial.PARITY_NONE,\
            stopbits=serial.STOPBITS_ONE,\
            bytesize=serial.EIGHTBITS,\
                timeout=0)

        rospy.init_node('LiDAR_Collision_Avoidance', anonymous=False)
        rospy.Subscriber('LiDAR_Collision_Avoidance' + '/Settings/' , Settings, self.Send_comand)

        self.rate = rospy.Rate(10)
        self.range_topic= rospy.Publisher('LiDAR_Collision_Avoidance' +  '/Ranges/',  Range, queue_size=100) 


        self.data = []
        self.Range_msg= Range()
        self.Range_msg.header.frame_id="LiDAR"
        self.Range_msg.min_range=10
        self.Range_msg.max_range=1200
        self.Range_msg.field_of_view=3.6*(2*np.pi/360)
        self.Range_msg.radiation_type=1

        self.br=tf.TransformBroadcaster()

    def Send_comand(self,msg):
        settings_msg ="/%d,%d,%d,%d,%d,0,/"%(msg.slave_id,msg.initial_tick,msg.final_tick,msg.frequency,msg.tick_step)
        self.ser.write(settings_msg.encode())
        print("Send: " + settings_msg+"\n")


    def ReadRange(self):
        seq = []
        data = []
        config = False
        joined_seq=[]
        while True:
            for c in self.ser.read():
                #print(chr(c))
                if(chr(c)==","):
                    
                    if(config==True):

                        data.append(int(joined_seq))         
                        seq=[]
                else:
                    if (config==True):
                        seq.append(chr(c)) 
                        joined_seq = ''.join(str(v) for v in seq) 
                if(chr(c)=="/"):
                    if (config==True):
                        return data

                    config = not config 



    def main(self):
        
        while not rospy.is_shutdown():
            self.data=self.ReadRange()
            #print(self.data)
            self.publishRanges()
            
        self.ser.close()

            

    def publishRanges(self):
        
        rad_ang=self.data[2]*(2*np.pi/4096)
        
        quater_array=tf.transformations.quaternion_from_euler(0,0,rad_ang)
        self.br.sendTransform((0.2,0,0.08),quater_array,rospy.Time.now(),"LiDAR","base_link")

        self.Range_msg.range=self.data[1]
        self.Range_msg.header.stamp=rospy.Time.now()

        self.range_topic.publish(self.Range_msg)


            
def start():
    LiDAR = LiDAR_Collision_Avoidance()
    LiDAR.main()


if __name__ == '__main__':
    try:
        start()
        rospy.spin()
    except rospy.ROSInterruptException:

        pass
         
    

    
